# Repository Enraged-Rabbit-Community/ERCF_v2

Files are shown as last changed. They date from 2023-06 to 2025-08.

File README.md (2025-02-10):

# Enraged Rabbit Community Project

<p align="center">
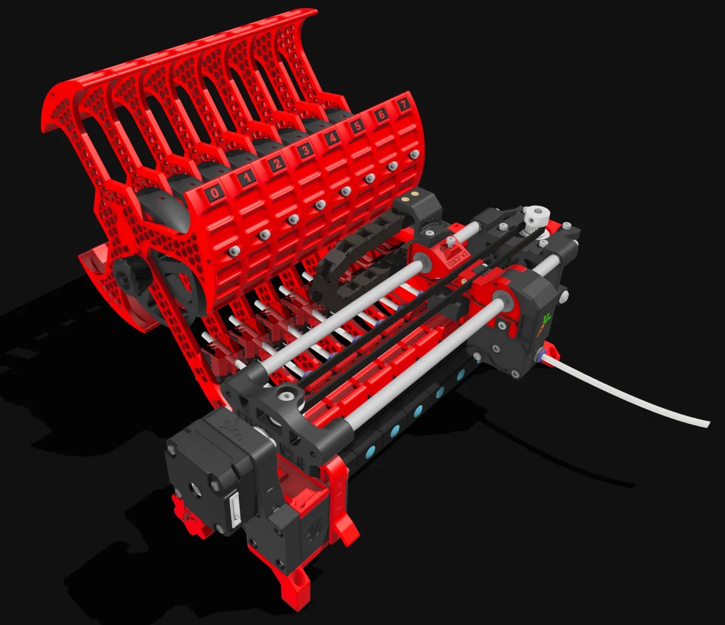
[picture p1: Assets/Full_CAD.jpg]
ERCFv2
  
  <h1 align="center">ERCF v2 - RC1</h1>
</p>

<p align="center">
An expandable MMU for Klipper-based 3D-Printers
</p>

<p align="center">
   &nbsp;
   &nbsp;
   &nbsp;
   &nbsp;
   &nbsp;
</p>

<br>

<table>
<tr>
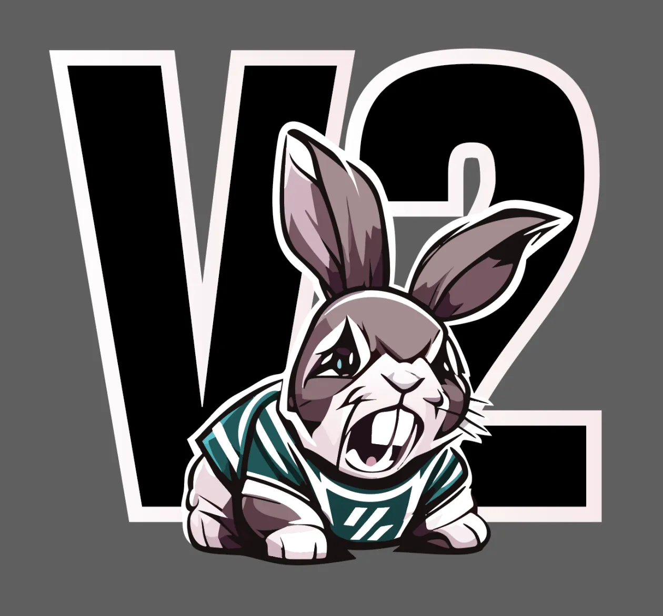
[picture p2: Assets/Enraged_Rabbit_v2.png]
RabbitV2
<td width=30%></td>
<td>
This is a community-born project and a major update to the Voron ERCF MMU that was started a couple of years ago by Ette.  It is endorsed by Ette, and the guiding philosophy wasn't to start again with a new MMU design but to refine what has already proven to be a very capable machine and push it to be the best it can be by simplifying problematic construction, improving reliability and aligning as close as possible to v1.1 BOM. However, the project includes an all-new optional integrated filament buffer system (ERCT), filament cutter option (ERF), a collection of recommended tool head sensor modifications and a bit of Bling! It fully leverages the Happy Hare firmware MMU control software with Klipper Screen extensions.
<p>
  
There is a rapidly growing list of MMUs in the marketplace, from the mass-produced "Fords" who pioneered the market to the "Toyota" that are more recent efficient engineering feat but somehow lacked soul. We consider ERCFv2 the "BMW" - a little over-engineered perhaps but distinctively cool, and you feel good driving it.  We hope you enjoy it! &nbsp;&nbsp; Videos: [Teaser](https://www.youtube.com/watch?v=U2QwvPacIUk) &nbsp; [Release](https://www.youtube.com/watch?v=EJCPerBsM3Q)
</td>
</tr>
</table>

## Table of Content
  
**[ERCF](#enraged-rabbit-carrot-feeder-ercf)**<br>
**[ERCT](#enraged-rabbit-cotton-tail-erct)**<br>
**[ERF](#enraged-rabbit-filametrix-erf)**<br>
**[Toolhead Sensor Modifications](#toolhead-sensor-modifications)**<br>
**[Firmware](#firmware)**<br>
**[Documentation](#documentation)**<br>
**[BOM](#bom)**<br>
**[CAD](#cad)**<br>
**[FAQ](#faq)**<br>
**[Acknowledgements](#acknowledgements)**<br>
**[Vendors](#vendors)**<br>
**[Changelog](#changelog)**<br>
**[Build Photos](#build-photos)**<br>
**[Showroom](#user-print-showroom)**<br>
<!--
**[FAQ](Assets/FAQ.md)
-->

<br>

## Enraged Rabbit Carrot Feeder (ERCF)
<table>
<tr>
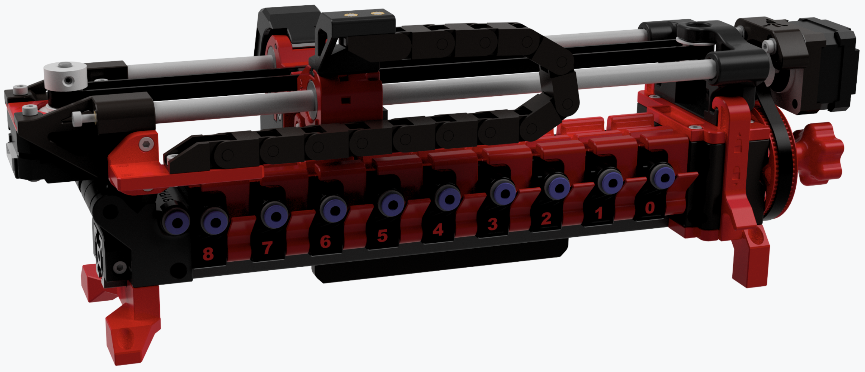
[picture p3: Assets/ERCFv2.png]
<td width=45%>An MMU or Multimaterial Unit/Upgrade allows for the automatic change of filaments on your 3D printer.  You can use it to create beautiful multi-colored prints or, if you're lazy, simply to avoid loading filament by hand. If you are familiar with ERCF v1.1, this will serve as an overview of updates:</td>
<td>
<ol>
  <li>Sturdy backbone - no more flex
  <li>Reliable (and custom) encoder design
  <li>Sprung servo instead of adjustable top hats
  <li>Innovative Filament trap in blocks instead of magnetic gates
  <li>Formal filament bypass
  <li>Reinforced gearbox assembly
  <li>Beautifully illustrated Manual
  <li>High Quality Step-by-step CAD
  <li>New integrated passive buffer system (Cotton Tail)
  <li>Perfect tips with Filametrix Filament cutter
  <li>Functional and aesthetic LED status indication
</ol>
</td>
</tr>
</table>

<br>

## Optional Enraged Rabbit Components

### Enraged Rabbit Cotton Tail (ERCT)
<table>
<tr>
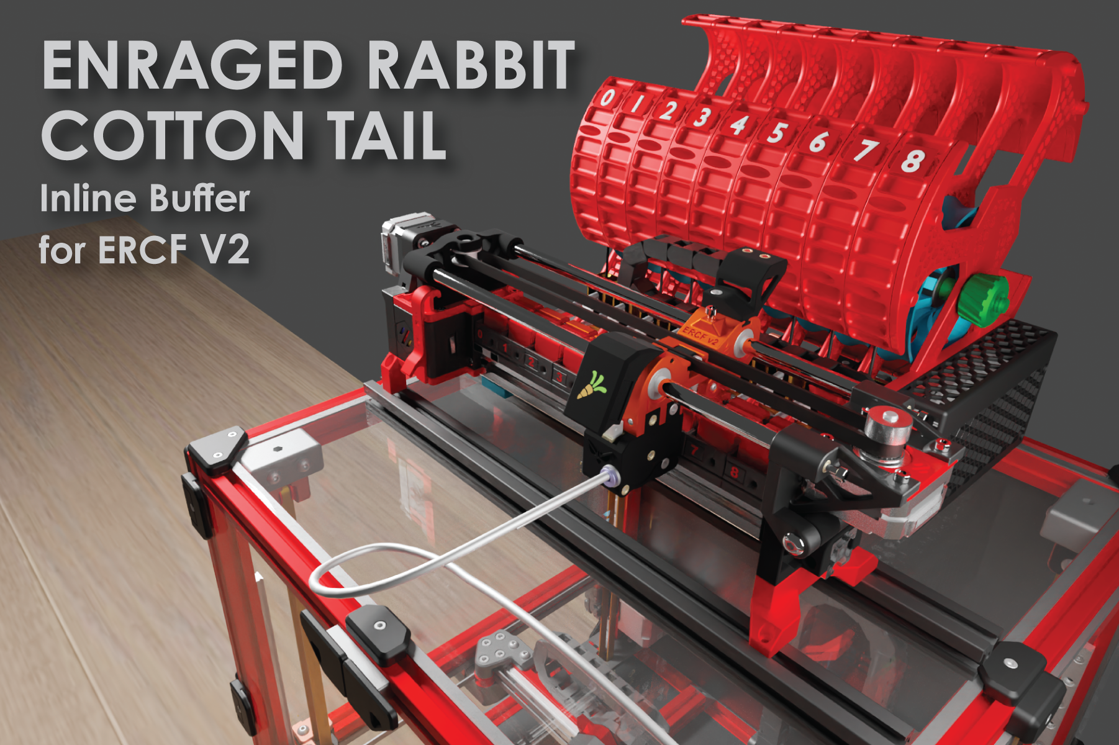
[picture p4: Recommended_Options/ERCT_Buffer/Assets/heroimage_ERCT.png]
ERCT
<td width=30%></td>
<td>
When an MMU changes tool, the unloaded filament needs to be thoughtfully managed so that it doesn't tangle. The Enraged Rabbit Cotton Tail (ERCT) buffer system is designed to attach directly to ERCF V2. It is a passive system that optimizes space and is also designed to reduce resistance in the filament path, creating a consistent system for calibration.
<p>

ERCT includes a pregate filament sensor to more reliably manage endless spools. It also incorporates a NEOpixel on each gate that, when driven by the Happy Hare firmware, provides functional feedback and the necessary "bling!" Enjoy!
<p>

[Read more](Recommended_Options/ERCT_Buffer/README.md) &nbsp;&nbsp; Videos: [Rear Loading](https://youtu.be/9jzB5Un6HKo) [Front Loading](https://youtu.be/GlSXtUkd-b8)
</td>
</tr>
</table>

<br>

### Enraged Rabbit Filametrix (ERF)
<table>
<tr>
<td>
Before the MMU can unload a filament, the tip must be prepared so that it can be cleanly loaded next time.  This tip-forming process is very difficult to tune and varies based on material type, temperature, hotend type and even weather!  Introducing Enraged Rabbit Filametrix (ERF) filament cutting system.  This lightweight addition to your Stealthburner toolhead adds a cutting blade.  When retracting, the problematic tip of the filament is simply cut off for perfect tips and no jams.
<p>

ERF also supports an optional servo operated ganrtry activation pin so no print area is lost with this addition. ERF designs also include the recommended integrated toolhead sensor
<p>

[Read more](Recommended_Options/ERF_Filament_Cutter/README.md)
</td>
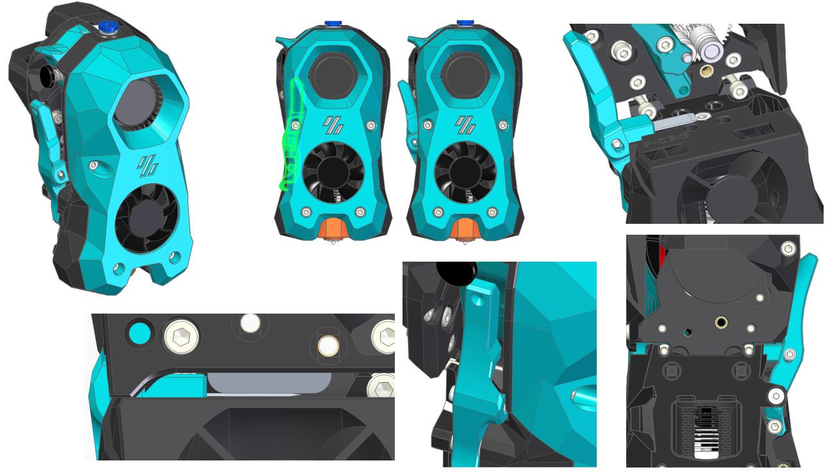
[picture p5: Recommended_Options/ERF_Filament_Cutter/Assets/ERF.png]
ERF
<td width=30%></td>
</tr>
</table>

<br>

### Toolhead Sensor Modifications
<table>
<tr>
<td>
ERCF can be operated without a toolhead sensor (filament detection) in the toolhead but it is **not recommended**. A toolhead sensor provides an accurate homing point very close to the nozzle but also adds reliability to the tool change process. ERCF includes a set of toolhead sensor modifications for popular extruders. These work reliably through coupling a microswitch to the filament path.
<p>

[Read more](Recommended_Options/Toolhead_Modifications/README.md)
</td>
</tr>
</table>

<br>

### Purge System (ERPS)
Pellet purge system to remove the need for the wipe tower. Stay tuned.

<br>

## Firmware
<table>
<tr>
<td width=30%>KlipperScreen</td>
<td>
ERCF is designed to be used with the Happy Hare MMU firmware for Klipper which adds a set of klipper extensions for configuration setup, testing and operation of ERCF. These commands are available through the command line or macros but are perhaps best operated with an interactive UI with the optional KlipperScreen extension.
<p>

Happy Hare provides an easy installation script which has knowledge of recommended settings and will greatly accelerate the setup process.
<p>

[Happy Hare](https://github.com/moggieuk/Happy-Hare/wiki) &nbsp;&nbsp; [KlipperScreen](https://github.com/moggieuk/KlipperScreen-Happy-Hare-Edition)
</td>
</tr>
</table>

<br>

## Documentation
<table>
<tr>
<td>
Building something as complex as an MMU is a challenging undertaking, but the ERCFv2 project contains an amazingly detailed and illustrated manual with step-by-step instructions.  We have tried to make the process similar to fitting together a jigsaw puzzle, albeit with a few optional pieces.
<p>

[ERCFv2 PDF Manual](Documentation/ERCF_v2_Manual.pdf)
</td>
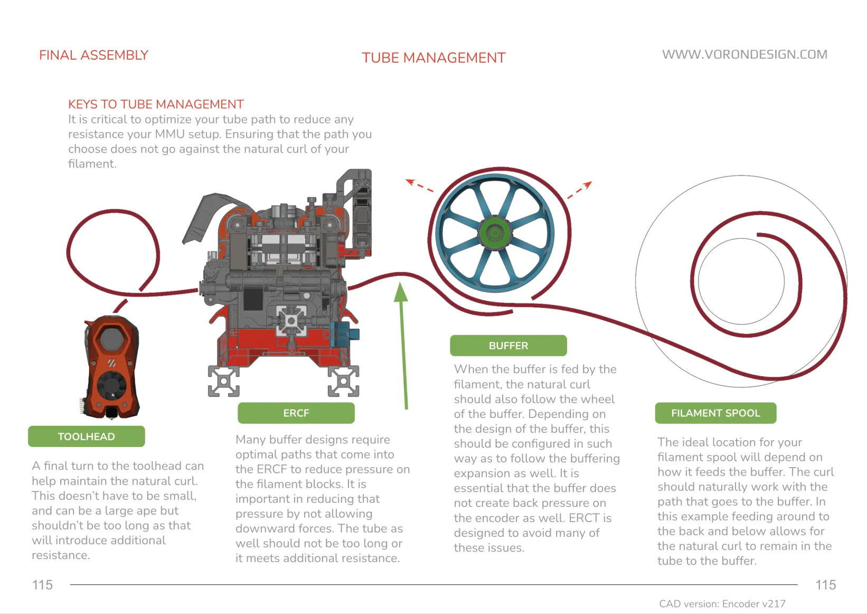
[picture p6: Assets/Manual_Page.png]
ERCF Manual
<td width=30%></td>
</tr>
</table>

<br>

## BOM
<table>
<tr>
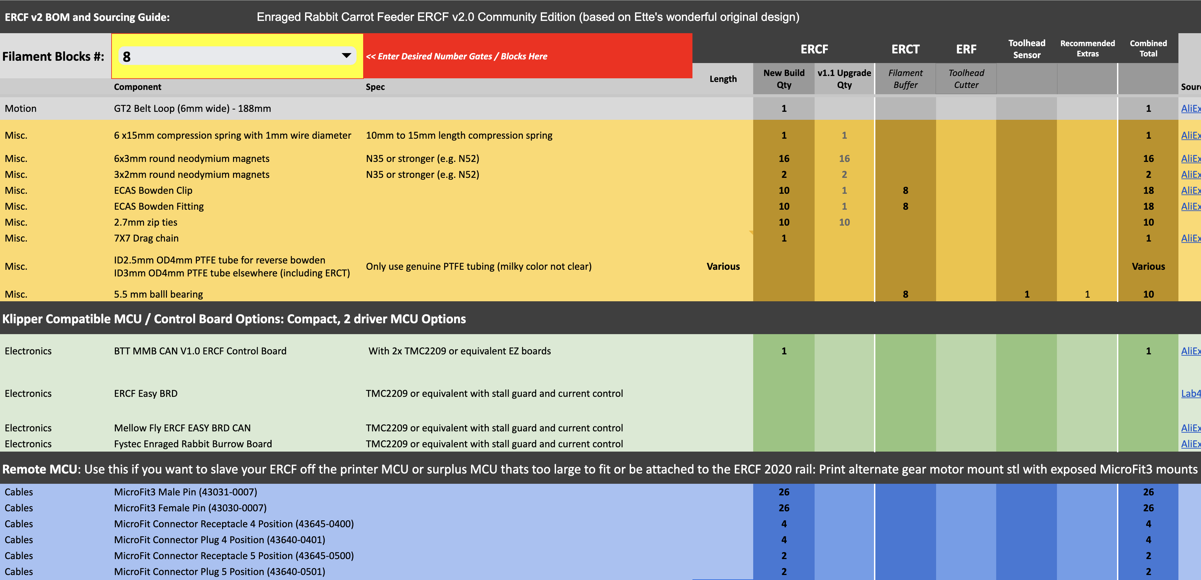
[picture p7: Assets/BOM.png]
ERCF Project BOM
<td width=30%></td>
<td>
You can find a Bill of Materials (BOM) and a convenient printed parts tracker for the project and options here. Note that the BOM also contains an upgrade list for those of you who want to use your existing ERCF v1.1 kits. Please make a copy and edit the "Filament Blocks #" to be the number of gates for your build.  This can be any number, but we encourage kit vendors to use 4/8/12 as size variations. Note that there are separate columns for core ERCF, the optional ERCT and ERF options, as well as the suggested "extras"
<p>
Please be aware that the BOM is strictly for reference. The recommended parts can be exchanged for other similar quality parts. Manufacturers who use the BOM as a reference must submit an application for certification before selling them as ERCF V2 kits. Please contact us for certification.

[BOM](https://docs.google.com/spreadsheets/d/1HtVIu4yqzS6xJQr63-JKtMAh4Xq7wbtWPFeuiCnrnnE) &nbsp;&nbsp; [Printed Parts Tracker](https://docs.google.com/spreadsheets/d/1h1bJurR6Z8Ou36c5U9cWmqI86tXKlWrcZrWrHgGN13A)
</td>
</tr>
</table>

<br>

## CAD
<table>
<tr>
<td>
A lot of work has gone into creating a quality CAD model of the project, carefully organized into folders that match the documentation!  It is highly recommended that you open the CAD and hide every folder and then expose them one at a time as you work through the build.
<p>

[Master CAD](CAD)
</td>
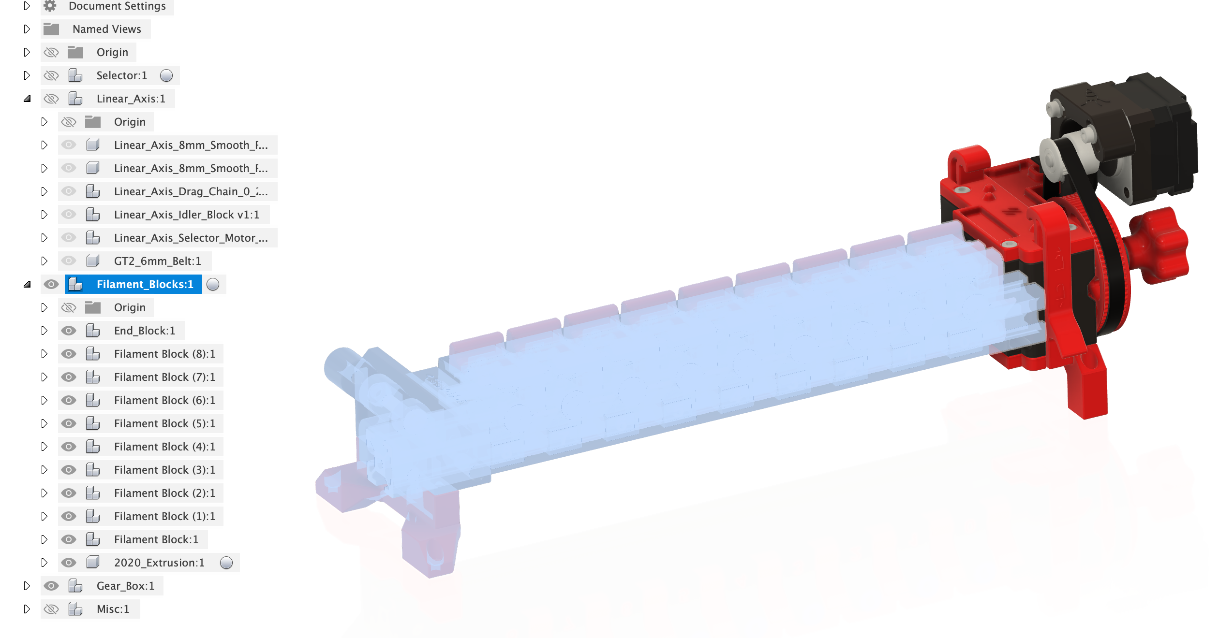
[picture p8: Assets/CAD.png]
ERCF Master CAD
<td width=30%></td>
</tr>
</table>

<br>

## FAQ
ERCF v2 is currently in the RC1 phase.  That means that we hope the BOM and parts are complete, but there are still some areas of polish needed: documentation, kit availability, etc. Therefore, we're sure there will be lots of questions.  To avoid repetition on the various support channels, you can find a list of [frequently asked questions](FAQ.md) here.  If something isn't answered the best place to go is the [ERCF Discord server](https://discord.gg/MPZ4cHm9gm)

<br>

## Acknowledgements
Most importantly let me introduce the development, test and doc team.  A project like this doesn't happen without many hundreds of hours of volunteer effort and all of these folks are truely awesome.  Please give some :clap: :clap: :clap:
<ul>
  <li>@moggieuk V0.1503 | V2.4088 (Mr Happy Hare & Chief whip)
  <li>@gneu V2.5345 (Filament block & bling innovator)
  <li>@sneakytreesnake V2.3804 (The project backbone!)
  <li>@mneuhaus VT.483 (Mr Binky)
  <li>@Miriax (Designer & Doc Demon)
  <li>@kinematicdigit VS.744 (Mr Cotton Tail & Doc Illustrator)
  <li>@ningpj (Tester, Breaker & Documenter)
  <li>@fizzy (King of CAD)
  <li>@gsx8299 (Test Builder Extraordinaire)
  <li>@sorted (Filametrix "don't get enraged" filament cutting system)
  <li>@kierantheman (Mr ThumperBlocks)
  <li>@Fragmon (Videographer)
  <li>@Silverback V2.1356 (Filametrix tester, builder & engineer)
</ul>

<br>

## Vendors
<table>
<tr>
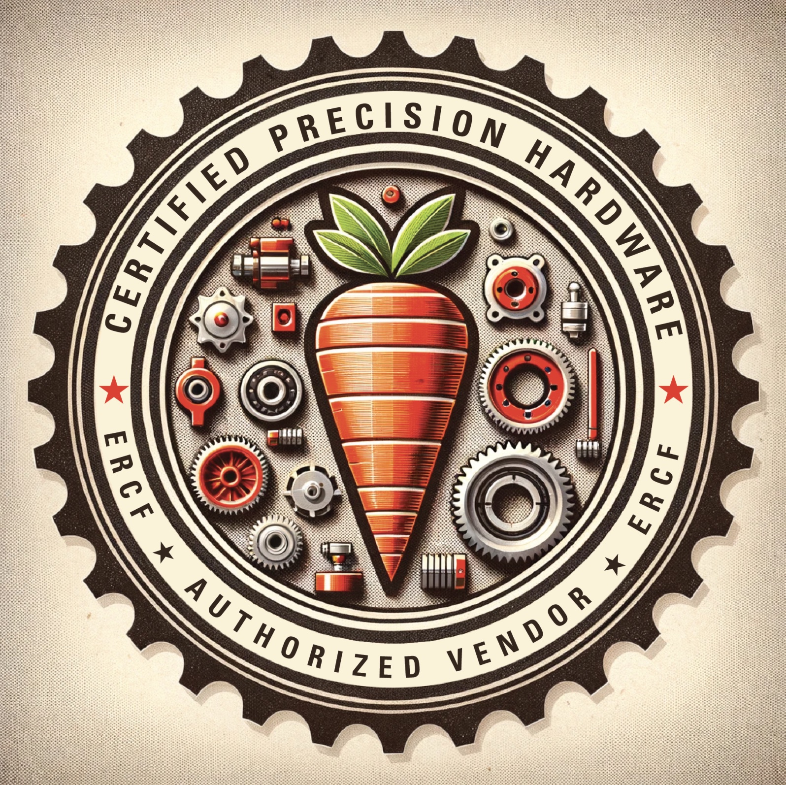
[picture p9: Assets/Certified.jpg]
Vendor Certification
<td width=25%></td>
<td>
These kits and specialty parts will have been checked by us and meet good quality standards. Pending Certification means it has met our first pass inspection and in the process of being verified as a V2 kit. <strong>WE DO NOT RECOMMEND PURCHASING KITS WITHOUT THE CERTIFICATION BY US. PLEASE CHECK BACK HERE FOR THE LIST OF AUTHORIZED VENDORS AND MANUFACTURERS</strong>:<br>
<p>
<ul>
  <li> <strong>Certified - Siboor</strong>
  </li>
  <li> <strong>Certified - Triangle Labs</strong>
  </li>
  <li> <strong>Certified - Seleadlabs</strong>
  </li>
  <li> <strong>Certified -  Makerpanda</strong>
  </li>
  <li> <strong>Certified -  Fysetc</strong>
  </li>
  <li> Pending Certification - LDO Motors
  </li>
  <li> <strong>Certified - Dodo 3D Labs</strong>
  </li>

  <br>
  <p>
  A list of more official and certified vendors is on the way... stay tuned!
</td>
</tr>
</table>

**Manufacturers:**
_If you want to be included, please contact us. We are happy to validate your kit/parts and then add you to the list._

<br>

## Changelog
<ul>
  <li>v2.0 rc1 - Initial Release (Merry Christmas!)
</ul>

CAD Design Guidelines used in this project (in case you were interested) can be found: [here](/Assets/Dev_Notes.md).

<hr>

<p align="center"><i>
There once was a printer so keen,<br>
To print in red, yellow, and green.<br>
It whirred and it spun,<br>
Mixing colors for fun,<br>
The most vibrant prints ever seen!
</i></p>

<br>

## Build Photos












<br>

## User Print Showroom
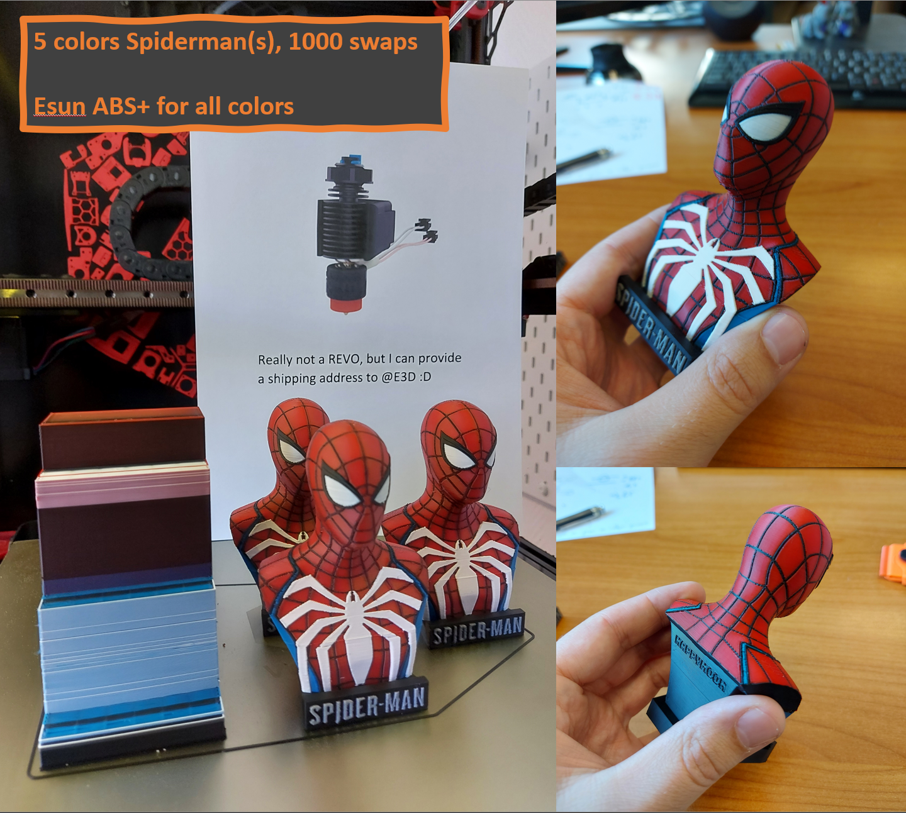
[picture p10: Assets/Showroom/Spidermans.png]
Spidermans
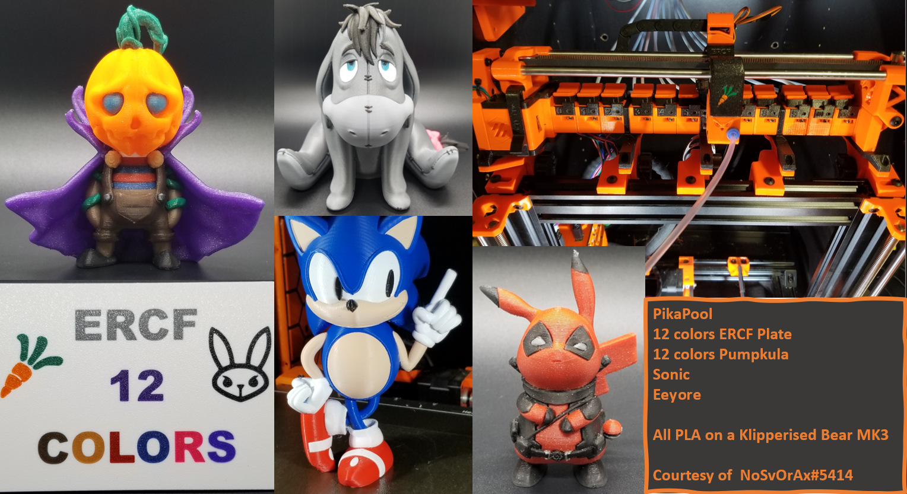
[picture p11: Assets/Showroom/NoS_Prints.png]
NoS_prints
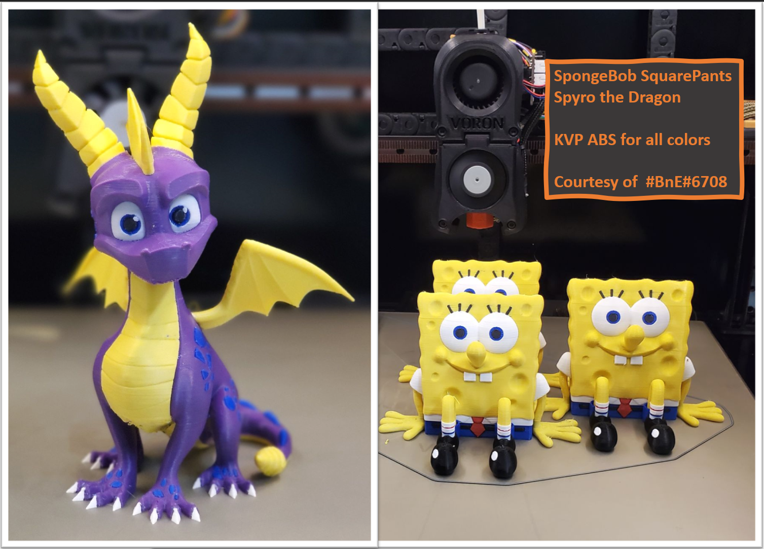
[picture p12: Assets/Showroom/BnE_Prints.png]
BnE_Prints
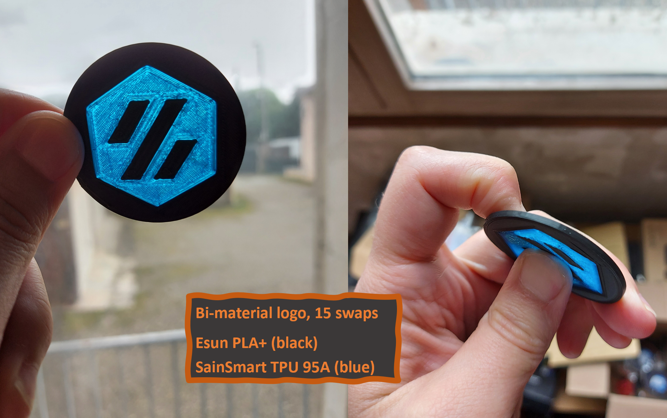
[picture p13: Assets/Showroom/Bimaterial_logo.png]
Voron Logo TPU
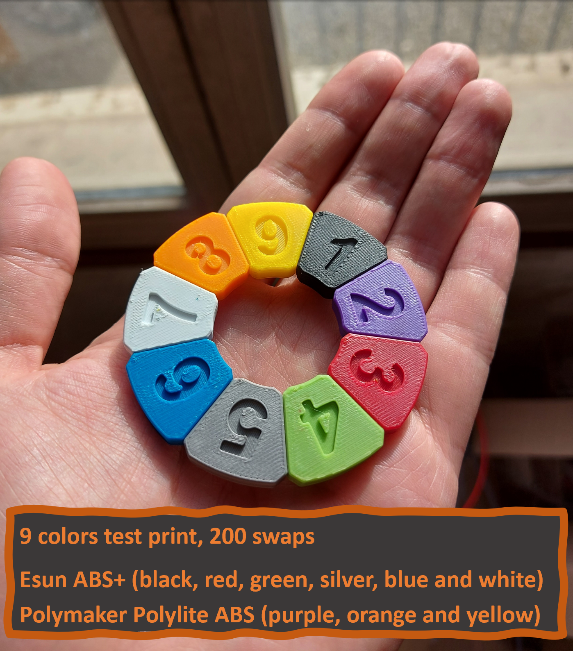
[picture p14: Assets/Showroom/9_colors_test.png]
9_colors_test


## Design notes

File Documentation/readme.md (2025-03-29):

# ERCF Quickstart

Follow the steps on these pages in order to set up ERCF for the first time!

### ERCF Setup Steps:
- [Flashing Your Local MCU](https://github.com/Enraged-Rabbit-Community/ERCF_v2/blob/master/Documentation/Flashing-Local-MCU.md)
- [Installing Happy Hare](https://github.com/Enraged-Rabbit-Community/ERCF_v2/blob/master/Documentation/Installing-Happy-Hare.md)
- [Happy Hare Configuration](https://github.com/Enraged-Rabbit-Community/ERCF_v2/blob/master/Documentation/Happy-Hare-Configuration.md)
- [Hardware Configuration Checks](https://github.com/Enraged-Rabbit-Community/ERCF_v2/blob/master/Documentation/Hardware-configuration-checks.md)
- [Hardware Calibration](https://github.com/Enraged-Rabbit-Community/ERCF_v2/blob/master/Documentation/Hardware-Calibration.md)
- [Toolhead Distances](https://github.com/Enraged-Rabbit-Community/ERCF_v2/blob/master/Documentation/Toolhead-Distances.md)
- [Installing KlipperScreen Happy Hare](https://github.com/Enraged-Rabbit-Community/ERCF_v2/blob/master/Documentation/Installing-KlipperScreen.md)
- [Slicer Setup](https://github.com/Enraged-Rabbit-Community/ERCF_v2/blob/master/Documentation/Slicer-Setup.md)
- [Further Mods to Consider](https://github.com/Enraged-Rabbit-Community/ERCF_v2/blob/master/Documentation/Further-Mods.md)

#### Even more Happy Hare info can be found at:
- [Happy Hare Wiki](https://github.com/moggieuk/Happy-Hare/wiki)

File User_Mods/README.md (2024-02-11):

# User mods

## Summary and Links

**Gneu42**
* [Block End with Bushing](Gneu42/Block_End_with_Bushings)
* [Drag chain Anchor with connectors](Gneu42/Drag_Chain_Anchor_With_Microfit3)
* [Selcetor Drag chain Anchor with servo connectors](Gneu42/Selector_Drag_chain_Anchor_with_servo_connectors)
* [Apron Leds Blank cover](Gneu42/Apron_Leds)

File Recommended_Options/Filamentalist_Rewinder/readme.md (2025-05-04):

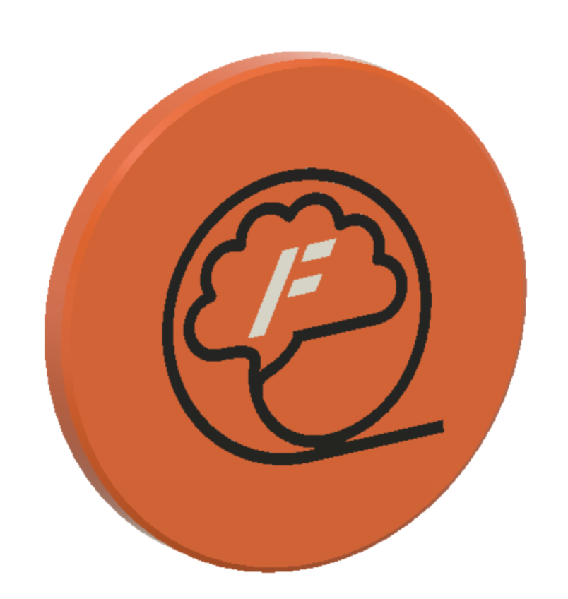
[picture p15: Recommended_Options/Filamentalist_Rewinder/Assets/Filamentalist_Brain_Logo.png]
<p align="center">
<h1 align="center">The "Filamentalist" Passive Filament Driven Rewinder</h1>

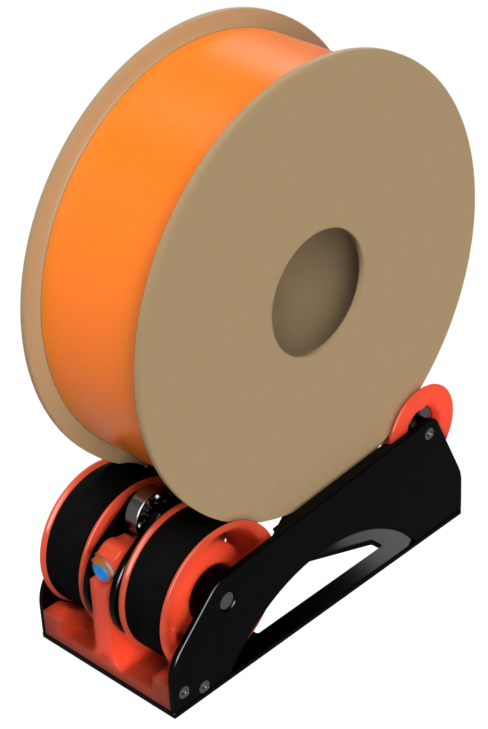
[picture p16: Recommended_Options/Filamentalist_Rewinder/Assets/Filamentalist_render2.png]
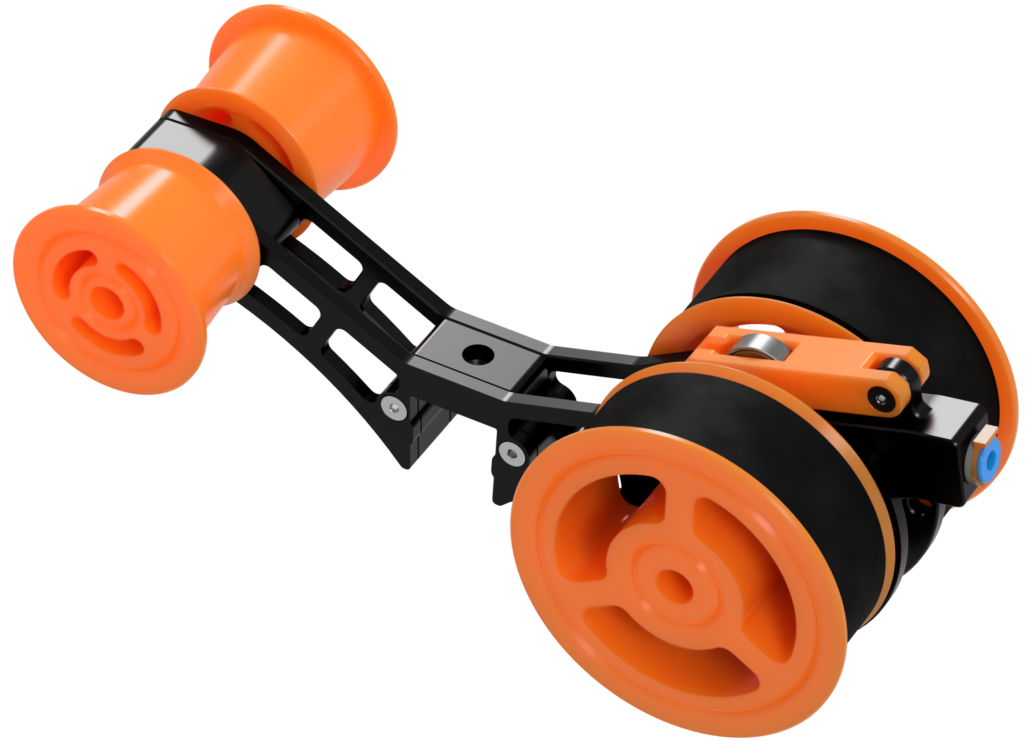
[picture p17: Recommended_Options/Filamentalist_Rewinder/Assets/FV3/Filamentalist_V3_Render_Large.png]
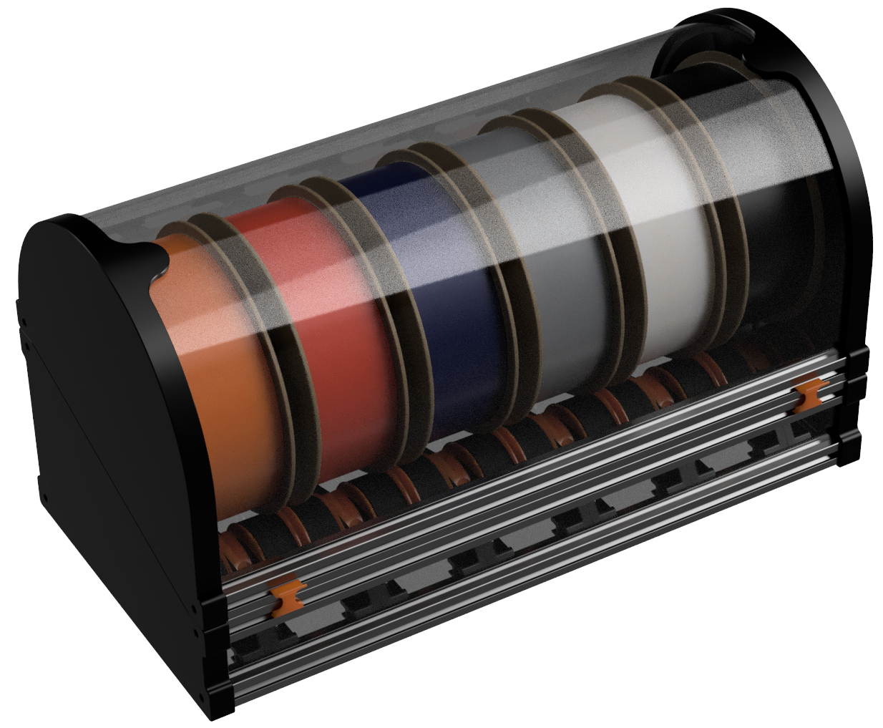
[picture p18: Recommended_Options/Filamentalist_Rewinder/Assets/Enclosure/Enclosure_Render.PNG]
[](https://github.com/Enraged-Rabbit-Community/ERCF_v2/tree/master/Recommended_Options/Filamentalist_Rewinder/Filamentalist_Classic_Rewinder)[](https://github.com/Enraged-Rabbit-Community/ERCF_v2/tree/master/Recommended_Options/Filamentalist_Rewinder/Filamentalist_FV3_Rewinder)[](https://github.com/Enraged-Rabbit-Community/ERCF_v2/tree/master/Recommended_Options/Filamentalist_Rewinder/Filamentalist_Enclosure)
</p>
   
## _____ [Filamentalist "Classic"](https://github.com/Enraged-Rabbit-Community/ERCF_v2/tree/master/Recommended_Options/Filamentalist_Rewinder/Filamentalist_Classic_Rewinder) _________ [Filamentalist FV3](https://github.com/Enraged-Rabbit-Community/ERCF_v2/tree/master/Recommended_Options/Filamentalist_Rewinder/Filamentalist_FV3_Rewinder) ___________[Filamentalist Enclosure](https://github.com/Enraged-Rabbit-Community/ERCF_v2/tree/master/Recommended_Options/Filamentalist_Rewinder/Filamentalist_Enclosure) ____
</p>

## Filamentalist Discord group [here:](https://discord.gg/zHGH9sXFVK) ##

##  Description & Theory of operation:

The Filamentalist is a passive (no motors or electronics required) integrated buffering and spool holding multi-material unit (MMU) solution.  It provides space savings and potential filament path reduction that comes with using paths from spool to buffer to MMU.

- The Filamentalist uses the axial force delivered by the MMU gear motor along the filament to load and unload to and from the filament spool.
- An adjustable spring clamp forces the filament against two o-rings that sit on the drive pulley to create a high traction interface for rotating the axle and filament spool.
- A one-way clutch style bearing locks against the drive shaft and rotates the filament spool to take up filament during an unload.
- For loading and print extruding, the clutch disengages allowing for effective free-spooling of the filament spool similar to a roller style spool holder.
- The difference in diameter of the filament driven clutched roller versus the larger rim roller that the filament spool sits on provides the needed gear ratio to produce enough rotations to take up, and unload a nearly empty or full filament roll.
- During unloading/buffering, to account for the varying diameter of a spool from full to empty, filament tension will cause the spring loaded arm to lift a small amount and release traction from the o-rings allowing slip to occur between the filament and the o-ring interface of the rewinder producing a dynamic, continuously modulating variable gear ratio (full spool = max slip, empty spool = no/minimal slip).

<p align="center">
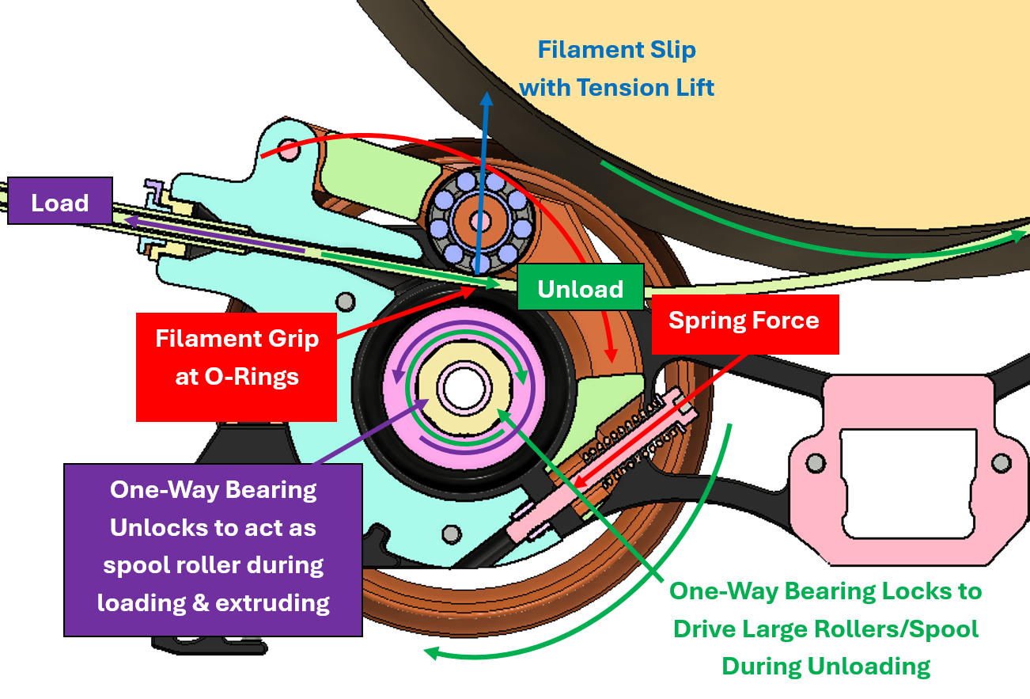
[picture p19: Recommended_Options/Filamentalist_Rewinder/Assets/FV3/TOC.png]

</p>

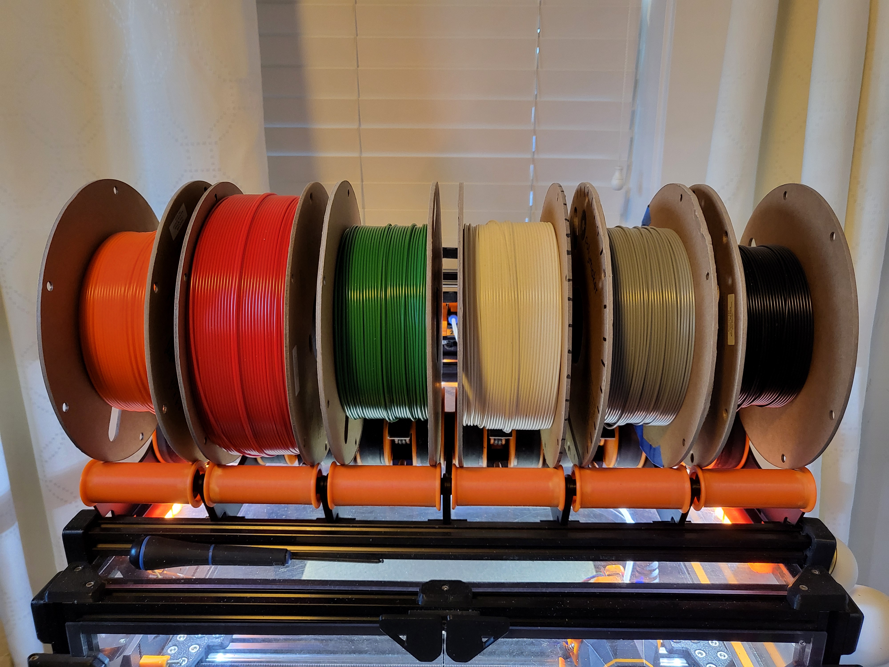
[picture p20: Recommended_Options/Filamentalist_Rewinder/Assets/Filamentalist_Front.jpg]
<p align="center">
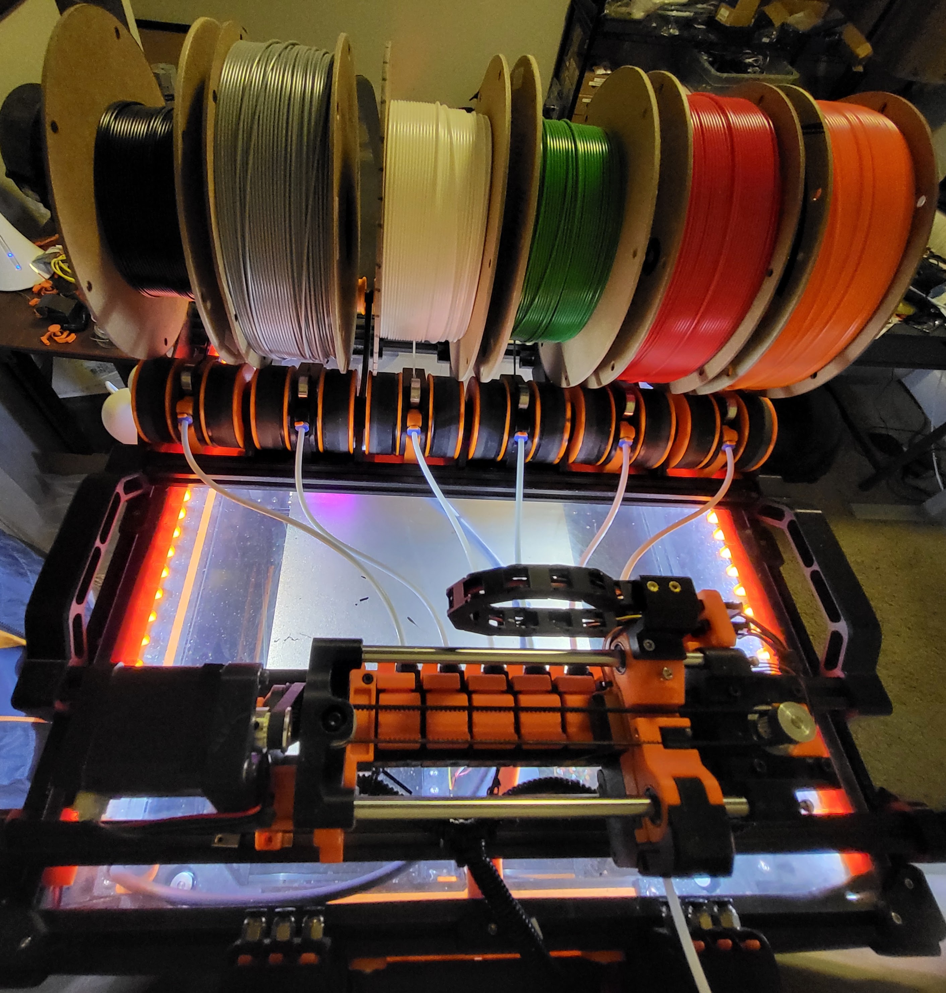
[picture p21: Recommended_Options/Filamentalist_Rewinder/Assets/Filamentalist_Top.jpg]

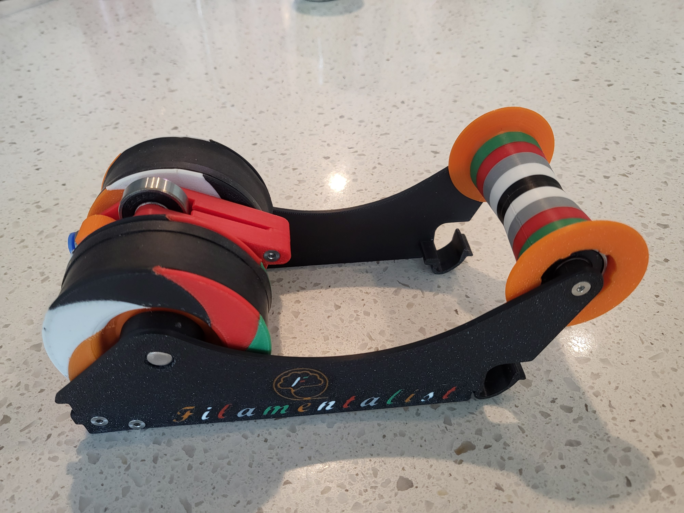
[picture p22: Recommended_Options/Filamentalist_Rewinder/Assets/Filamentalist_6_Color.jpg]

</p>

## Filamentalist Version Selection ##

One version is not necessarily better than the other.  The Filamentalist Classic has slightly better Tensioner system geometry making it a bit smoother in the filament grip/slip modulation.  The FV3 is "sexier" and accomodates wider spool widths in less horizontal space which can be useful for fitting in existing enclosures or across the top of a printer.  Below is a selection table to help with your decision.

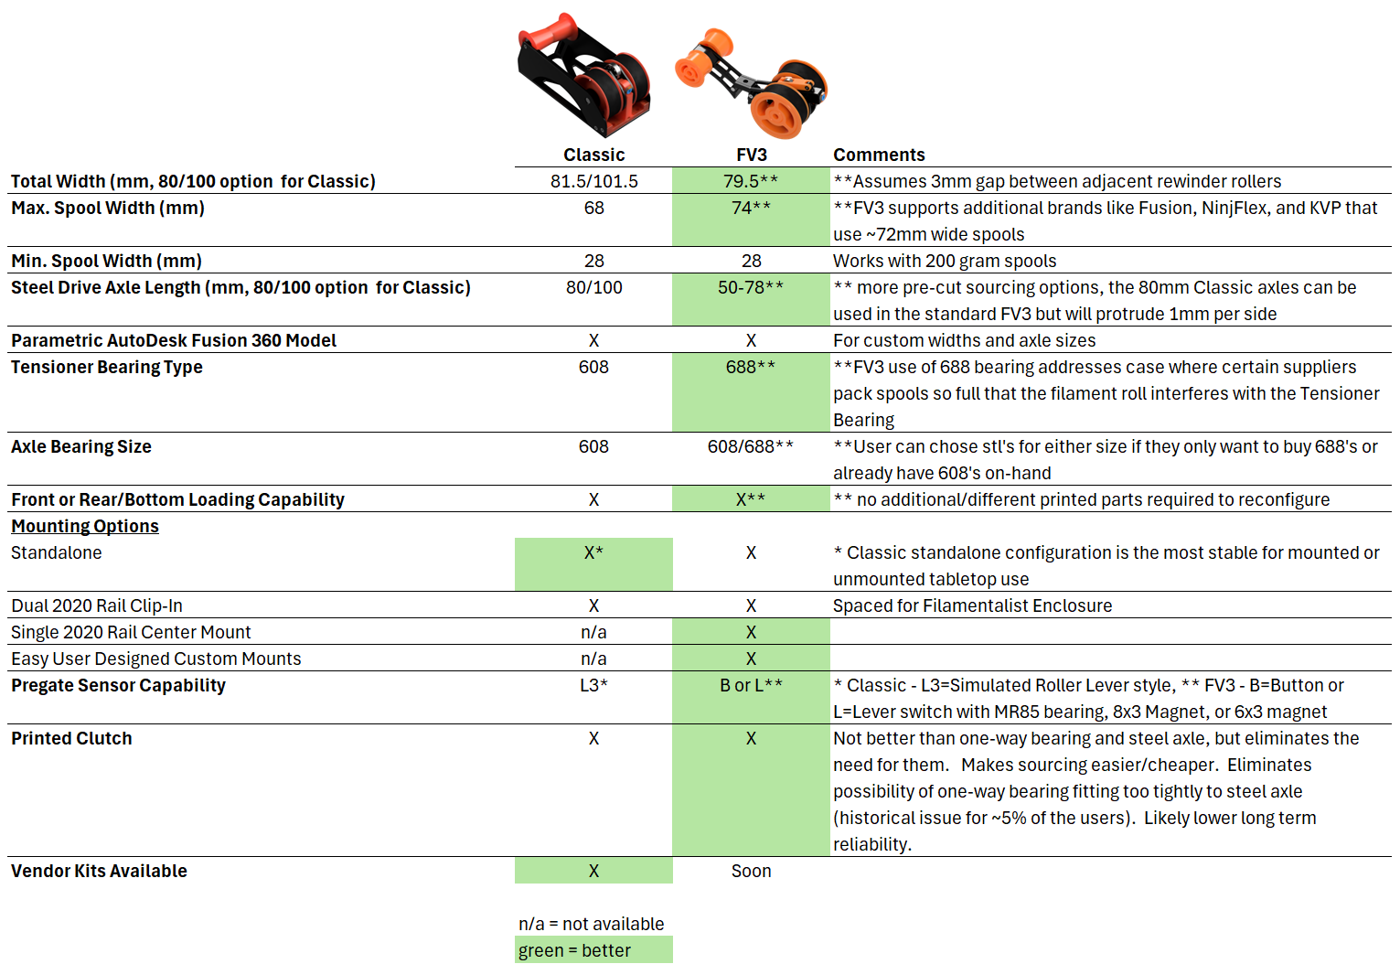
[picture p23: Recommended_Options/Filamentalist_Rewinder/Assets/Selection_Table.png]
<p align="center">

## Video of 6 rewinders swapping (plus SW Only Blobifier Purging):  [](https://photos.app.goo.gl/hKso7JYPZcdRLKrW8)

## [Video of loading a spool (pre-gate sensors auto-detect filament and pull into ERCF):](https://photos.app.goo.gl/yGS7Rr49dFMvjNLF9)  [](https://photos.app.goo.gl/yGS7Rr49dFMvjNLF9)

##  Credits:
Discord user Thisiscam first made me aware of [Muzi Xiaoyang's video](https://www.bilibili.com/video/BV1ZM41197fX/?spm_id_from=333.337.search-card.all.click) of a filament driven rewinder .  Through a long collaboration with Thisiscam, a great Beta dev/test team, and many design iterations/improvements on the Muzi Xiaoyang design, the Filamentalist was born. Key changes to the Muzi Xiaoyang design include incorporation of a one-way bearing, establishing the correct gear ratio for operation across the range of empty-to-full spools, and the long-life o-ring based filament clamping interface.

A special mention and thanks goes out to Cheesefrog and JCPhlux for their innovation and inputs for design refinement. 

##  **Additional Notes/Considerations** 

Things that you need to know include:
1. Due to continual evolution of the design based on user feedback, the pictures in the readme files and documentation may not always reflect the most current designs.  They will be similar and generally represent the latest parts and assemblies.
2. There are multiple options for the Filamentalist.  Determine which versions/options you want and select the stl's to print accordingly.  If you use Autodesk Fusion 360 there is parametric models available for both the Classic and FV3 rewinders that will allow customization for unique widths and axle lengths. Please see the Selection Aid table above to help choose.
3. If you're using, or upgrading from a ERCFv1 or v2 version you may want/need a higher torque gear motor.  Many in the Beta team ran NEMA 17's spec'd at 55 N-cm max torque and config'd them for 1-1.5A (probably overkill...).  If running the ERCF V1 or V2 with the 80 tooth gear Grafton's [40 Tooth NEMA 17 Mod](https://www.printables.com/model/692720-ercf-40-tooth-gear-modifiction) is a good modification for gaining more speed from a motor with 40N-cm torque or greater.  This may not be required so if you already have built your ERCF, try the Filamentalist with the motor/gearing you have and decide if you think you need more torque/speed.
4. Because the standard tuning of this design relies on some filament slip at the o-rings, the o-rings may ultimately wear-out.  Testing and extrapolation estimates that the wear-out point is  greater than 5K cycles. See the O-Ring Replacement section in the assembly manuals for o-ring swap/replacement instructions. 
5. Due to pressfits for the axle bearings and ECAS fitting, printer calibration is important.  Calibration "Test Block" stl's are included in the projects/CAD.  It is recommended you print the calibration tool first and test the press fits, M3 thread cutting, M3 slip fit, filament path holes to determine if you need to apply any scaling or changes to your extrusion factors in your slicer before printing.  Due to varying ECAS supplier tolerances and varying printer tolerances some experienced cracking at the ECAS hole when pressing in the ECAS.  If all other press fits work well on the calibration tool but you experience cracking at the ECAS hole when pressing in an ECAS fitting, you can use an Xacto knife to lightly remove some plastic from the ECAS hole.  If the ECAS is too loose you can use superglue to glue the ECAS into the Tensioner Mount (not the Test Block 😉 ).
6. Questions or input?
   - Refer to the [FAQ](https://github.com/Enraged-Rabbit-Community/ERCF_v2/blob/master/Recommended_Options/Filamentalist_Rewinder/Filamentalist_FAQ.md)
   - [Troubleshooting Guide](https://github.com/Enraged-Rabbit-Community/ERCF_v2/blob/master/Recommended_Options/Filamentalist_Rewinder/troubleshoot.md)
   - Filamentalist Discord group [here:](https://discord.gg/zHGH9sXFVK)

##  Tuning

Tune by setting the Tensioner Arm clamping force.  The arm does not need an extreme amount of tension.  To tune the spring force, lift the tensioner and insert a section of filament through the o-ring bearing interface and into the bowden tube.  Hold a Rim Roller to keep it from rotating and try to pull the filament out (in unload direction).  You want the slip force to be slightly more than what the overall system drag is, so you have to imagine the range of gear motor pull force vs rewinder drag and set a slip range in-between the two "imaginary" lines.  As a starting point adjust the spring tensioner screw accordingly and err on the light side.  Run the rewinder (see test code below). If loose filament is forming around the filament spool during unload, tighten the spring tensioning screw.  If no loose filament is forming around the filament roll, gradually reduce the spring tension until loose filament starts to accumulate and then increase tension in ~1/2 screw turn increments until you feel you have the lightest tension that results in a tightly packed unload. 

##  Testing

Below are macros you can cut and paste into the bottom of your mmu_software.cfg or printer.cfg to test and tune your rewinders.

Happy multi-material printing and rewindering!

```
[gcode_macro rewinder_test]
gcode:
    {% set tool = params.TOOL | default(0) | int %}   ; This target can be set with the drop-down in Mainsail
    {% set cycles = params.CYCLES | default(5) | int %}   ; This target can be set with the drop-down in Mainsail
    {% set speed = params.SPEED | default(300) | float %}   ; This target can be set with the drop-down in Mainsail
    {% set accel = params.ACCEL | default(300) | float %}   ; This target can be set with the drop-down in Mainsail
    {% set length = params.LENGTH | default(800) | float %}   ; This target can be set with the drop-down in Mainsail

    MMU_SELECT TOOL={tool}
    MMU_PRELOAD
    MMU_TEST_LOAD LENGTH=50
    {% for n in range(cycles) %}

        MMU_SERVO POS=DOWN
        MMU_TEST_MOVE SPEED={speed} ACCEL={accel} MOVE={length}
        MMU_SERVO POS=UP
# to stop a macro mid-cycle you must use the e-stop.  This dwell allows you to hit the e-stop while the servo is up so that you can pull the filament out of the ERCF while the printer/macro is stopped
        MMU_SERVO POS=DOWN
        MMU_TEST_MOVE SPEED={speed} ACCEL={accel} MOVE=-{length}
        MMU_SERVO POS=UP

    {% endfor %}

    MMU_UNLOAD

```

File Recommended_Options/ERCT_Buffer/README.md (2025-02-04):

# Enraged Rabbit Cotton Tail

<p align="center">
  ERCT
</p>

## Introduction

The Enraged Rabbit Cotton Tail (ERCT) buffer system is designed to attach directly to ERCF V2. It is also designed to reduce as much resistance as possible in the filament path, creating a consistent system for calibration.

This system is also designed to reduce the buffer length, while the loops are defined by the amount of tube you use from the encoder to the tool head. This is calculated by the total Bowden tube length divided by 225.  QoL features also allow for illuminated coupler blocks to indicate filament states.

**Features include:**

* Large central buffer wheel - reduces the bend radius of the filament's natural shape - each wheel comes pre-notched to make loading filament easier.
* Inline connection - connects directly to the 2020 extrusion arm
* Short Buffer Length - Can operate as short as 500mm in buffer Length
* Stackable Arm - Each arm is stackable for whatever combination of gates you want. They are optimized for strength and lightweight while providing loading and unloading filament access. More than 12 channels will require self-sourcing a metal axle rod, but printing your own up to 12 channels is available in the STL directory.
* Uses most parts from ERCP V1 -  if you already have a kit, most parts should be interchangeable.

##

***

## Acknowledgements

ERCT was designed to simplify the buffer design and integrate cleanly with ERCFv2. I thank the entire team from the ERCF V2 team, especially Moggie, for bringing me onto the team. I also have my home server, Fizzy's Tech, on Discord to thank for the countless support and hosting of the Beta development on that server. Jose from Fizzy's Tech was instrumental in this development as he was part of the system's early development and early testing. There are numerous testers who have helped as well, making suggestions throughout the beta cycle. I want to give a special shout-out to Wolffy01 and gsx8299 for their contributions to ideas, testing and mods.&#x20;

Questions related to this buffer can be directed at <https://discord.com/channels/460117602945990666/909743915475816458> or you may visit my home server at <https://discord.gg/Gs2vAtK7T7>

Terrance Lam
@kinematicdigit
###

***

### BOM (Each arm group/channel):

* (4) 8mm M3 screws
* (1) 16mm M3 screw
* (1) M3 threaded inserts (M3x5x4mm) Heat Sets
* 48.5mm PTFE Tubing (4mm OD/3MM ID Clear)
* (1) 608 ZZ Bearing (same as ERCP - skateboard bearings will work as well)
* (2) ECAS
* (1) M3 Roll-in Spring T-nut (for attaching to 2020 extrusions)

### End cap (with integrated MMB CASE) needs:

* (5) 8mm M3 screws
* (4) M3 threaded inserts (M3x5x4mm) Heat Sets

* (1) BTT MMB Can board
* (1) Microswitch per arm
* (1) 5.5 mm ball bearing per arm
* (2) 8 or 10 mm M2 self-thread screws per arm
* (1) Button Neopixels per arm
***

**FULL BUILD INSTRUCTIONS FOUND IN THE ERCF V2 BUILD GUIDE**

**LOADING THE BUFFER**

There are several ways to load the buffer. Use this as a reference but you may find other ways to load that is easier for you.

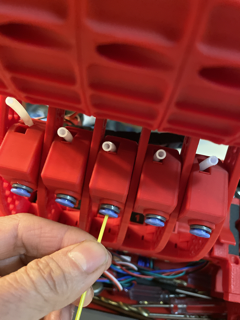
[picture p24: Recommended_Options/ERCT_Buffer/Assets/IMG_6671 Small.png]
|  | To load the buffer, filament from your reverse Bowden. Try your best to work with the natural curl of the filament and feed it till you see it pop out on top. |
| ---: | :--- |
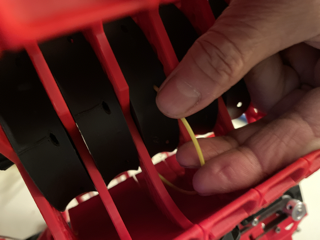
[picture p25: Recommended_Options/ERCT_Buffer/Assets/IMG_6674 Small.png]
|  | Grab it from up top, and curl it back into one of the multiple filament loading holes located along one side of the buffer wheel. |
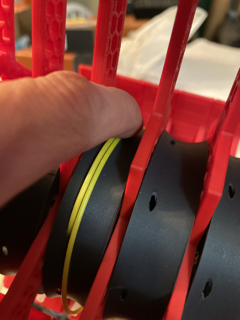
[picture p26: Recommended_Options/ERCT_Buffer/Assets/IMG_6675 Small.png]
|  | Turn the wheel until you have the number of rows needed for your tube length between the ERCF encoder and the tool head (to calculate the right length, measure the tube and divide by 230mm. This will equal the number of rows you need to wrap around the wheel - maximum of 7). |
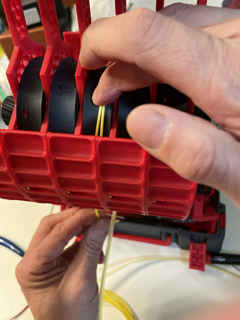
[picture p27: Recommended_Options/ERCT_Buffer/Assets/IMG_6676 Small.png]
|  | Back below, grab the filament on the wheel and pull it out. |
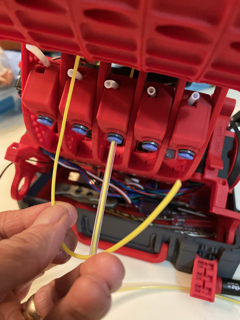
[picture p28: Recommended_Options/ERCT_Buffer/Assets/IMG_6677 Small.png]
|  | Give yourself some length (about 30 cm). |
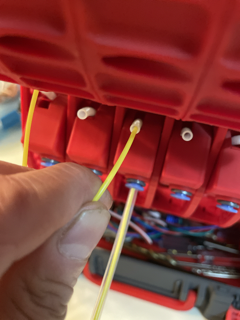
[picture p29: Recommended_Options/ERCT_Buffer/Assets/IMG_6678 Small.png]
|  | Feed back into the tube located there. |
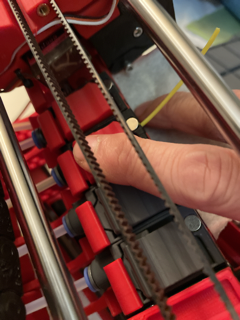
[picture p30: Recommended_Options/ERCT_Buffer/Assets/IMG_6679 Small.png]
|  | It will feed through, and you should feel some resistance from the trap; press on the top hat to help it through. |
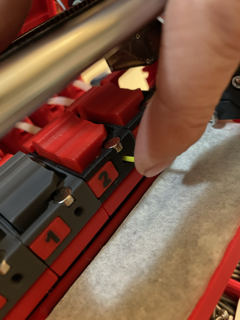
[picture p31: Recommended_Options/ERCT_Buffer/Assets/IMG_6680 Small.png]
|  | The final step is to push the filament flush to the opening so it doesn’t catch on the selector. That’s it. Load it all up, and away you go! |

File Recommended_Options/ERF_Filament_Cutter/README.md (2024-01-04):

# Enraged Rabbit "Filametrix" Filament Cutter
<table>
  <tr>
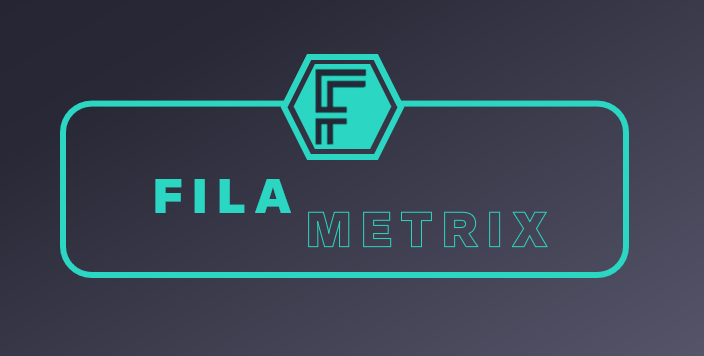
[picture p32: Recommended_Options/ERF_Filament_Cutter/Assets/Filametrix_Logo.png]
ER Filametrix
    <td width=30%></td>
    <td>
      This options adds a lightweight filament cutting capability to the Voron Stealthburner CW2 toolhead for perfect filament tips without having to tune the traditional tip forming process. Thanks to contributors it supports a number of different hotends. This can lead to much greater reliability of your MMU.  We hope over time to offer support for additional toolheads.
    </td>
  </tr>
</table>

<br>

## Illustration

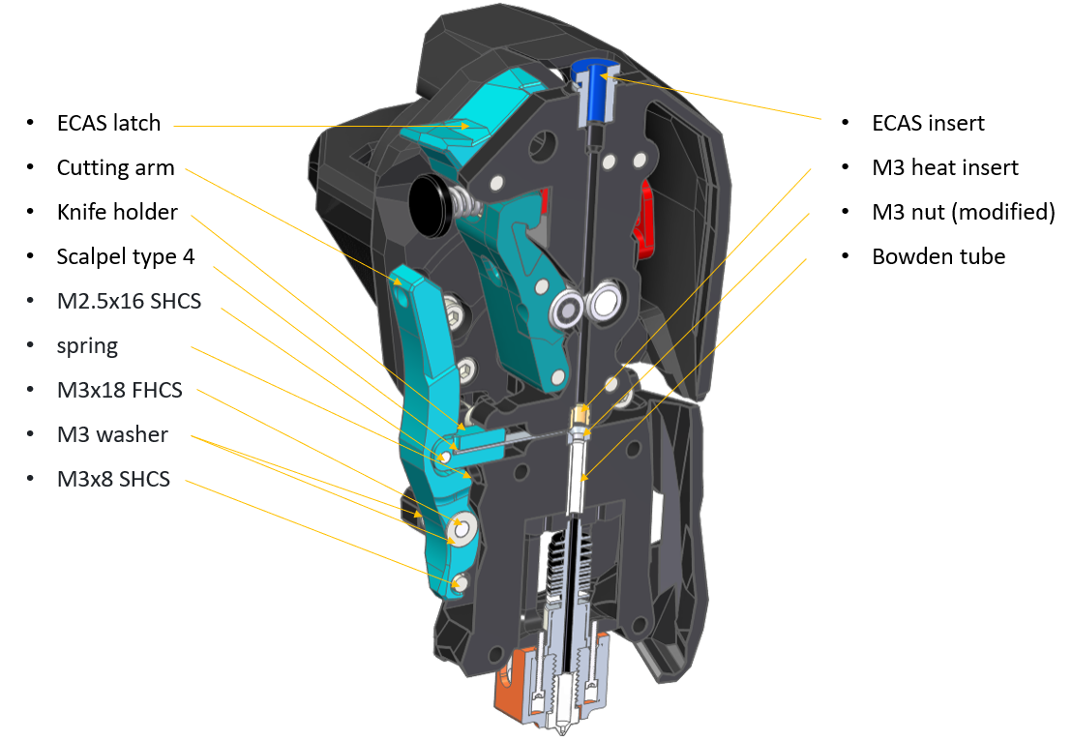
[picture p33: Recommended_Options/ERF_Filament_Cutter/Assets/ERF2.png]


## Toolheads
Currently ERF is only available for the Stealthburner toolhead. We hope to offer other options in the future. When choosing toolhead sensors "types" refer to the explanation of options [here](/Recommended_Options/Toolhead_Modifications/README.md#possible-options-explained).

### Supported Extruders for StealthBurner and Sensor Options
<table>
  <tr>
    <th>Extruder</th>
    <th>Sensor Option</th>
    <th>STLs</th>
    <th>Credit</th>
  </tr>
  <tr>
    <td rowspan="4">Clockwork2 (CW2)</td>
    <td>1_Toolhead_And_Entry_Sensors</td>
    <td><a href="Stls/1_Toolhead_And_Entry_Sensors/SB_CW2_Body.stl">Body</a></td>
    <td rowspan="4">Credit: <a href="https://github.com/juliusjj25">juliusjj25</a></td>
  </tr>
  <tr>
    <td>2_Toolhead_Sensor (EBB Board)</td>
    <td><a href="Stls/2_Toolhead_Sensor/SB_CW2_Body_EBB.stl">Body</a></td>
  </tr>
  <tr>
    <td>3_Entry_Sensor</td>
    <td><a href="Stls/3_Entry_Sensor/SB_CW2_Body.stl">Body</a></td>
  </tr>
  <tr>
    <td>4_No_Sensors</td>
    <td><a href="Stls/4_No_Sensors/SB_CW2_Body.stl">Body</a></td>
  </tr>

  <tr>
    <td>LGX Lite</td>
    <td>4_No_Sensors</td>
    <td><a href="Stls/4_No_Sensors/SB_LGX_Lite_Body.stl">Body</a></td>
    <td>Credit: <a href="https://www.printables.com/de/model/576122-lgx-lite-stealthburner-filament-cutter">tommorox234</a></td>
  </tr>
</table>

### Supported Hotends for StealthBurner

<table>
  <tr>
    <th>Hotend</th>
    <th>STLs</th>
    <th>Credit</th>
  </tr>
  <tr>
    <td>V6-R6<br><a href="Stls/Hotends/V6_R6/">Repo</a></td>
    <td>
      <ul>
        <li>SB_V6_R6_Cutting_Printhead_Back.stl
        <li>SB_V6_R6_Cutting_Printhead_Front.stl
      </ul>
    </td>
    <td></td>
  </tr>
  <tr>
    <td>Rapido<br><a href="Stls/Hotends/Rapido/">Repo</a></td>
    <td>
      <ul>
        <li>SB_Rapido_TH_Cutting_Printhead_Rear.stl
        <li>SB_Rapido_TH_Cutting_Printhead_Front.stl
      </ul>
    </td>
    <td>
      <p>Credit: <a href="https://github.com/juliusjj25">juliusjj25</a>
    </td>
  </tr>
  <tr>
    <td>Dragon<br><a href="Stls/Hotends/Dragon/">Repo</a></td>
    <td>
      <ul>
        <li>SB_Dragon_Cutting_Printhead_Back.stl
        <li>SB_Dragon_Cutting_Printhead_Front.stl
      </ul>
    </td>
    <td></td>
  </tr>
  <tr>
    <td>Revo Voron<br><a href="Stls/Hotends/Revo/">Repo</a></td>
    <td>
      <ul>
        <li>SB_Revo_Voron_Cutting_Printhead_Back.stl
        <li>SB_Revo_Voron_Cutting_Printhead_Front.stl
      </ul>
    </td>
    <td> Credit: Russell Gower </td>
  </tr>
  <tr>
    <td>Bambu<br><a href="Stls/Hotends/Bambu/">Repo</a></td>
    <td>
      <ul>
        <li>SB_Bambu_Cutting_Printhead_Back.stl
        <li>SB_Bambu_Cutting_Printhead_Front.stl
        <li>SB_Bambu_Adaptor.stl
        <li>SB_Bambu_Adaptor_M5_Nut.stl
      </ul>
    </td>
    <td>Credit: Jakub Kadlec (Facebook)</td>
  </tr>
  <tr>
    <td>Slice Mosquito<br><a href="Stls/Hotends/Mosquito/">Repo</a></td>
    <td>
      <ul>
        <li>Slice_Mosquito_Cutting_Printhead_Front_And_Rear.stl
      </ul>
    </td>
    <td>Credit: <a href="https://www.printables.com/de/model/614813-filametrix-mod-for-slice-engingeering-mosquito-hot">MakeAUsername_285162</a></td>
  </tr>
</table>
</details>

<br>

## How it works

Proof of concept [Video 1](https://youtube.com/shorts/HOMG8cVk_U4)

Proof of concept [Video 2](https://youtu.be/tTcrxttyths)

Filametrix [in action](https://www.youtube.com/watch?v=tfMZWQRqtvY)

<br>

> [!NOTE]  
> - You will need to use one of the ADXL mounting threads
> - Careful placement of the cutting point will minimize impact (if any) to build area.  Note that a gantry servo option is available for operating the "Depressor Pin" to ensure no impact

<br>

## What you need
### Print list
#### Toolhead
- 1x SB (hotend name) Cutting Printhead Back
- 1x SB (hotend name) Cutting Printhead Front
- 1x SB Main body Cutting with ECAS (with selected sensors)
- 1x SB motor plate (as Stealthburner has seen a small update the newest plate does not fit anymore. So please use the one from this git)
- 1x SB Latch ECAS
- 1x Cutting Arm
- 1x Knife Holder

#### Cutting point on gantry
- 1x Depressor Mount
- 1x Depressor

#### Cutting point on gantry with servo
- tbd...

### Parts list - considering you already have a Stealthburner with Dragon Hotend

#### Toolhead: 
- Loctite
- 1x M3 nut (DIN934; idealy a countersunk tool to modify the nut for proper filament insertion)
- 2x M3 washer (0.5mm)
- 1x M3x18 SHCS (it repleaces the top left M3x25 SHCS from the SB-Cover mount) 
- 2x Voron heat inserts
- 1x M3x18 FHCS (counter sunk screw)
- 1x M3x8 SHCS
- 1x M2.5x16 SHCS (15-18mm works)
- Spring 0.4x4x15 or alternative of ballpoint pen (L=15mm; D<=4,5mm) (I've ordered some for testing, to have a "defined" spring)
- Type 4 metal hobby blades (we will cut it to length) [Link](https://de.aliexpress.com/item/1005005117830095.html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) Amazon link, these need glue to be held in but work fine (USA) [Link](https://www.amazon.com/dp/B07QP8L1QG)

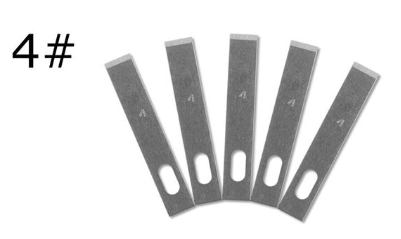
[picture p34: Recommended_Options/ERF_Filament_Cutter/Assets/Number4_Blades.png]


#### Cutting point on gantry
- 1x M3x16 BHCS
- 1x M3 nut
- 1x M3x8 FHCS
- 2x M3 SHCS (Lengths: 6mm - no backers, 10mm - titanium backers, 12mm - MGN9 rails)
- 2x Voron heat inserts

<br>
<hr>

## Assembly
### Cutting arm
<table>
  <tr>
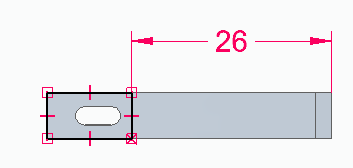
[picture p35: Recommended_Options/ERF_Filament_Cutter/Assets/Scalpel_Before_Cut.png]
Scalpel Before Cut
    <td width=40%></td>
    <td>Cut scalpel to length l=26mm</td>
  </tr>
  <tr>
    <td width=40%>Scalpel After Cut</td>
    <td>After cut</td>
  </tr>
  <tr>
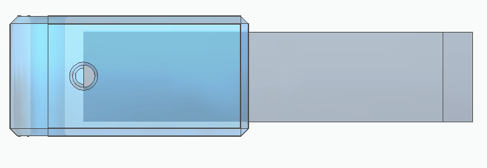
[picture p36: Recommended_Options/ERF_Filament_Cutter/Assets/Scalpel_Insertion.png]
Scalpel Insertion
    <td width=40%></td>
    <td>Insert scalpel into knife holder</td>
  </tr>
  <tr>
    <td colspan=2>Insert the scalpel (which is cut to 26mm) into the knife holder until you see it in the little hole. Use pliers to push it into the knife holder. Some force should be needed as the scalpel should stay in place due to the "pressfit". If that's not the case add some glue.(Depending on scalpel tolerances)</td>
  </tr>
  <tr>
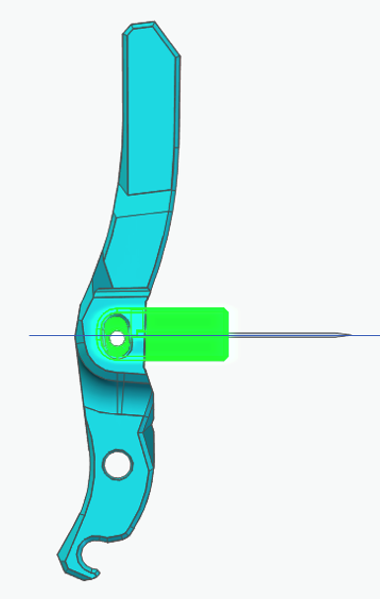
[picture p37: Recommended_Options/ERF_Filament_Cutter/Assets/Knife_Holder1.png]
Holder1
    <td width=40%></td>
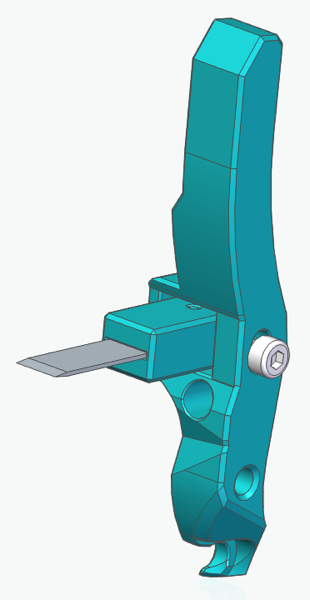
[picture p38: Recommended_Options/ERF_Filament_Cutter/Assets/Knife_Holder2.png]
Holder2
    <td></td>
  </tr>
  <tr>
    <td colspan=2>Put knife holder into cutting arm. The M2.5x15 screw is directly screwed into the plastic of the knife holder. The tip of the screw should be flush with the cutting arm or no more than 0.1-0.3mm above it. Check the orientation of the hole for the M2.5 screw in the knife holder. It needs to be on the bottom side.</td>
  </tr>
</table>

> [!NOTE]  
> The knife holder must move up and down without friction in the cutting arm but shoult not have a lot play. Maybe some grinding is needed.

### Toolhead Body
<table>
  <tr>
    <td width=40%>SB Main Body</td>
    <td>Add heat inserts. Tip here for the heat set that goes above the cutter - suggest drilling the threads out with a ~2.5mm drill bit. On the hotend holder side below the cutter make sure you flare out the PTFE tube to help guide the filament.</td>
  </tr>
  <tr>
    <td width=40%>SB Cutting Printhead</td>
    <td>SB cutting Printhead back</td>
  </tr>
  <tr>
    <td width=40%>Depressor</td>
    <td>Depressor - one on either end, end with ribs should be flush with surface below ribs with no plastic sticking up past surface</td>
  </tr>
  <tr>
    <td width=40%>Depressor</td>
    <td>Finished cutting point assembly should look like this. Note: for titanium backers, the backer should be centered between belt clamps and the end of the depressor mount should be flush with the end of the backer. This will work for all backers with 10/20/40mm spacing with the furthest back hole 5-15mm from the end. Height of depressor should be adjusted to press in the depression on the cutting arm and the BHCS can be adjusted in and out for the right positioning and locked in place with the M3 nut</td>
  </tr>
</table>

<br>

## Happy Hare Setup

### In mmu_parameters.cfg:

`form_tip_macro: _MMU_CUT_TIP` to instruct Happy Hare to use the filament cutter rather than normal tip forming.

Make sure `toolhead_extruder_to_nozzle` and `toolhead_sensor_to_nozzle` are set to your particular toolhead as per the Happy Hare documentation.

`force_form_tip_standalone: 1` this tell Happy Hare to always use the tip cutting macro.

> [!IMPORTANT]  
> Make sure you turn off tip forming or any extruder movements in your slicer - the slicer must not take any part in the filament swap. It should pick up when purging the new filament to the purge block.

### In mmu_filamentix.cfg:
Configure the `_MMU_CUT_TIP` macro variables as per the instructions in the file.

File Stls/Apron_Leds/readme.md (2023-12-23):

# Apron Neopixels

The neopixel holder is designed to snap on the 2020 extrusion just under each gate. It consists of a Holder and a cover. One of each per gate.
## what to print ?
* **2 holders are available :**
  * One for a strip of LED 10mm wide.
    * **Holder_Strip_Leds_xN.stl**
  The same is used to light the chamber of the Voron printers with a spacing of 16.5mm. It can be found on aliexpress. We used the RGBNW, 1m 60 IP30, Black PCB <br> https://fr.aliexpress.com/item/32476317187.html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
  * The second is designed to hold the individual neopixel RGBW LED.
    * Holder_PCB_Led_xN.stl
  Those are the same neopixels used in the stealthburner.
  The holders are printed standing up with an (optional) brim ears STL : Holder_Brim_ears_xN.stl<p>
* **2 versions of the covers are  provided :**
  * One that print flat but need supports (**recommended**).
    * **Cover_Body_xN.stl**
    * **[t]_Cover_Lens_xN.stl**
    
  * One that print standing up with no supports.
    * Options/Cover_Body_No_support_xN.stl
    * Options/[t]_Cover_Lens_No_support_xN.stl

The recommended STLs are :
  *  Holder_Strip_Leds_xN.stl because strip leds are much easier to solder and install.
  *  Cover with support. They give a better look especially on the lens part that can be printed with concentric(filled) top and bottom infill :
     *  **Cover_Body_xN.stl**
     *  **[t]_Cover_Lens_xN.stl**

## Tips

**Printing tips.**
* Holder can be print in any color. It is not visible.
* Cover_Bodies should be printed with opaque filament.
* Cover_lenses should be print with transparent filament.
* Load both files together into the slicer.
     Answer "Yes" to the mulicolor print dialog box.
* Select the color of your choice for the body, and transparent for the lens. 
    
* Add bottom and top infill pattern settings to the lens, and select concentric(filled) pattern. 
   
   Slice and print.
**Installation of the recommended STLs**
* Cut N individual LED form the strip, and tin all the solder pads.
* Snap all the holders on the 2020 extrusion under the filament blocks.
  * one side of the tang that snaps to the extrusion does not go up to the end. This is made to accommodate for the roll in nuts.
  * If for some reason you have a roll in nuts on both side of the holder, the opposite site can be cut off. 
* Stick each individual strip in the holder.
* Solder thin rigid wires between the strips.
* On gate 0 solder 3 wire that will go the RGB pin of the controller.
  * a small opening on each corner of the holders is used to pass the wires through.
  * At the last gate you can also solder 3 wires if you plan to add more RGB LEDs.
  * Snap the covers on the holders.

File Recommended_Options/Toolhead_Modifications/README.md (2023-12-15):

# Enraged Rabbit toolhead filament detection

This page explores the various options available for Toolhead Filament detection that is used by your MMU firmware to ensure reliable filament loading and to spot errors that might occur during the filament's loading and unloading processes. The ERCFv2 team advocate the utilization of a toolhead sensor only or dual-sensor system. In this section, you will find a comprehensive collection of standalone sensor options compatible with popular toolheads.

> [!IMPORTANT]  
> **Secured bowden**: It is important to ensure the bowden tube can't accidently separate from either the MMU or the toolhead. This is essential when opting for no toolhead sensors. We recommend secure fastening using a Push-Fit or ECAS connection. We wish to highlight that there are certain toolheads, such as the stock CW2, where the Bowden tube is simply inserted without any additional securing mechanism. Such setups present a heightened risk of the bowden tube dislodging from its holder and thus we offer a no-sensor version of these toolheads.

> [!NOTE]  
> **Using a filament cutter toolhead**: For users who have integrated the ERF filament cutter into their systems, please refer to the toolhead modifications outlined in then [ERF Filament Cutter](../ERF_Filament_Cutter/README.md) section where you will find a similar set of toolhead modifications but including the cutting option.

<br>

_____________________________

## Possible Options Explained
Position of the sensor
<p><em>Position of the sensor</em></p>

### **1. Toolhead and Entry Sensor**  
This setup allows the firmware (Happy Hare) to quickly load bowden and optionally home prior to extruder, then home to toolhead sensor before loading to the nozzle. The entry sensor also allow for easier calibration of the bowden length.  The twin sensors also allows for precise location of the filament in an error situation which increases the chances of automatic recovery. The downside is that you need two switch inputs to your MCU. **This is the luxury option.**  
   
✔ smooth bowden loading<br>
✔ precise extruder loading<br>
✔✔ great error recovery (excellent through precise filament location)

### **2. Toolhead Sensor only**  
With this setup the firmware can quickly load close to the nozzle and then precisely home to the toolhead sensor inside the extruder. The presence of the toolhead sensor is highly valuable in a MMU so the firmware allowing detection of correct behavior, smooth loading and auto recovery. This is usually an easy setup to accomodate and many toolhead boards or MCUs provide for this input. This option has a small possibliy of the filament not being detected as trapped between extruder and sensor but this is rarely a problem in practive. **This is the most common recommended option.**  
  
✔ smooth bowden loading<br>
✔ precise extruder loading<br>
✔ good error recovery (with in-extruder detection)

### **3. Entry Sensor only**  
With this setup the firmware can quickly load the bowden and home to a point close to the nozzle. Because the filament has not yet passed into the extruder there are inaccuracies that can occur during this transistion. Also this option has no way of knowing the filament is inside the extruder in error recovery situations and thus relies on additional user interaction.
     
✔ smooth bowden loading<br>
✘ extruder loading can be inprecise<br>
✘ poor error recovery (no way to determine if filament is inside extruder)

### **4. No Sensor**  
This setup has no sensors and is thus not recommended but it can be used if you have not other options with Happy Hare. It does include a secure bowden connection (ECAS or push fit) which is essential because the filament will be colliding with the extruder entrance. **This works but is not recommended.**  
  
✘ rough bowden loading that can fail (this system relies on collision detection when the filament hits the extruder)<br>
✔ extruder loading precision is reasonable<br>
✘ poor error recovery (there is no way to assertain the filament position)
_____________________________
 
## Recommend Mods
Here are the STLs for popular Toolhead/Extruder combinations.  Note that this is a compiled list and we invite you to help flesh out the rest...

<details open>
<summary><strong>Expand for Stealthburner Options</strong></summary>
<table>
  <tr>
    <th>Extruder</th>
    <th>1. Toolhead &amp; Entry Sensor</th>
    <th>2. Toolhead Sensor</th>
    <th>3. Entry Sensor</th>
    <th>4. No Sensor</th>
  </tr>
  <tr>
    <td>Clockwork 2</td>
    <td> <a href="./Stls/1_Toolhead_And_Entry_Sensors/[a]_SB_CW2_Latch.stl">Latch</a> <br> <a href="./Stls/1_Toolhead_And_Entry_Sensors/SB_CW2_Body.stl">Body</a> <br> <a href="./Stls/1_Toolhead_And_Entry_Sensors/SB_CW2_Plate.stl">Plate</a> <br> <sub>Additional items: <br> 1x ECAS <br> 2x D2F-5 <br>2x ball 5,5mm <br> 4x self tapping screw M2x10 <br> Credit: <a href="https://www.printables.com/model/466692-stealthburner-cw2-filament-sensors-with-ecas-latch">Petr Kašpar</a></sub> </td>
    <td> <br> <sub>Additional items: <br> 1x ECAS <br> 1x D2F-5 <br>1x ball 5,5mm <br> 2x self tapping screw M2x10</sub> </td>
    <td> <br> <sub>Additional items: <br> 1x ECAS <br> 2x D2F-5 <br>2x ball 5,5mm <br> 4x self tapping screw M2x10</sub> </td>
    <td> <a href="./Stls/4_No_Sensors/SB_CW2_Latch.stl">Latch</a> <br> <a href="./Stls/4_No_Sensors/SB_CW2_Body.stl">Body</a> <br> <sub>Additional items: <br> 1x ECAS</sub> </td>
  </tr>
  <tr>
    <td>Orbiter 2</td>
    <td></td>
    <td></td>
    <td></td>
    <td></td>
  </tr>
  <tr>
    <td>LGX Lite</td>
    <td></td>
    <td></td>
    <td></td>
    <td></td>
  </tr>
  <tr>
    <td>Galileo 2</td>
    <td></td>
    <td></td>
    <td></td>
    <td></td>
  </tr>
  <tr>
    <td>other extruder</td>
    <td></td>
    <td></td>
    <td></td>
    <td></td>
  </tr>
</table>
</details>

<details>
<summary><strong>Expand for XOL2 Options</strong></summary>
<table>
  <tr>
    <th>Extruder</th>
    <th>1. Toolhead &amp; Entry Sensor</th>
    <th>2. Toolhead Sensor</th>
    <th>3. Entry Sensor</th>
    <th>4. No Sensor</th>
  </tr>
  <tr>
    <td>Clockwork 2</td>
    <td></td>
    <td></td>
    <td></td>
    <td></td>
  </tr>
  <tr>
    <td>Orbiter 2</td>
    <td></td>
    <td></td>
    <td></td>
    <td></td>
  </tr>
  <tr>
    <td>LGX Lite</td>
    <td></td>
    <td></td>
    <td></td>
    <td></td>
  </tr>
  <tr>
    <td>Galileo 2</td>
    <td></td>
    <td></td>
    <td></td>
    <td></td>
  </tr>
  <tr>
    <td>other extruder</td>
    <td></td>
    <td></td>
    <td></td>
    <td></td>
  </tr>
</table>

</details>
<details>
<summary><strong>Expand for other toolhead options</strong></summary>
<table>
  <tr>
    <th>Extruder</th>
    <th>1. Toolhead &amp; Entry Sensor</th>
    <th>2. Toolhead Sensor</th>
    <th>3. Entry Sensor</th>
    <th>4. No Sensor</th>
  </tr>
  <tr>
    <td>Clockwork 2</td>
    <td></td>
    <td></td>
    <td></td>
    <td></td>
  </tr>
  <tr>
    <td>Orbiter 2</td>
    <td></td>
    <td></td>
    <td></td>
    <td></td>
  </tr>
  <tr>
    <td>LGX Lite</td>
    <td></td>
    <td></td>
    <td></td>
    <td></td>
  </tr>
  <tr>
    <td>Galileo 2</td>
    <td></td>
    <td></td>
    <td></td>
    <td></td>
  </tr>
  <tr>
    <td>other extruder</td>
    <td></td>
    <td></td>
    <td></td>
    <td></td>
  </tr>
</table>
</details>

_____________________________

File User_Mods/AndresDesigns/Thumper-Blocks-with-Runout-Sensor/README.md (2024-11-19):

# Thumper Block with integrated Runout Sensor

This mod adds support for filament presence detection using a D2F-style switch. The author doesn't use GitHub so you can find the project here: https://www.printables.com/model/1053193-thumper-block-with-integrated-runoutsensor

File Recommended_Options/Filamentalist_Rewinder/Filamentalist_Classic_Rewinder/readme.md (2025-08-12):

<p align="center">
<h1 align="center">The Filamentalist "Classic" Passive Filament Driven Rewinder</h1>

<p align="center">]
</p>
   
## [Filamentalist Classic Assembly Guide Document](https://github.com/Enraged-Rabbit-Community/ERCF_v2/blob/a68bc6678bab41d7bded5e42a17276a9430a0f45/Recommended_Options/Filamentalist_Rewinder/Filamentalist_Classic/Do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)  [](https://github.com/Enraged-Rabbit-Community/ERCF_v2/blob/a68bc6678bab41d7bded5e42a17276a9430a0f45/Recommended_Options/Filamentalist_Rewinder/Filamentalist_Classic/Do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)

## [Filamentalist Classic Assembly Guide Video](https://youtu.be/-1cHOcnosxE?si=RZV318OI9f3f_CkE)  [](https://youtu.be/-1cHOcnosxE?si=RZV318OI9f3f_CkE)

##  **BOM:**

**ATTENTION!! PLEASE READ COMMENTS IN FAR RIGHT COLUMN** (you may need to scroll over in your view)

| Qty per Site | Part | Example Source Reference | Comments |
|---|---|---|---|
| 1 | 8mm dia. x 80mm Stainless Steel Dowell Pin | https://www.amazon.com/uxcell-Stainless-Chamfered-Support-Elements/dp/B0BC8VFSWD, Amazon Alternate https://www.amazon.com/Unifizz-Stainless-Steel-Round-Silver/dp/B09P9MC953?th=1 (sheared ends may need to be cleaned up), Aliexpress https://www.aliexpress.us/item/3256801518620991.html | Undersized shaft (7.93-7.97mm or 5/16" dia) works the best.  100mm length is more available and can extend out of rewinder, you can cut polished 8mm or 5/16" diameter stainless rod to length, or there are stls to make a wider rewinder based on a 100mm axle.  Custom rewinder widths are also possible using the Fusion 360 parametric model and you can cut shaft to whatever length is desired. 8mm (or 5/16") diameter straight stainless tube is also an excellent alternative to solid rods as the are much easier to cut to length. |
| 5 | MR608 bearings | Can be obtained anywhere (Home Depot, Amazon, Aliexpress, etc.)  | MR608-2RS style recommended, but open or  MR608-ZZ style will work |
| 1 | HF081412 One-Way Bearing | https://www.amazon.com/dp/B0C7TRFJBS, Aliexpress | 8mm Bore, 12mm length, 14.2mm Diameter. Get the "octogonal" style. |
| 1 | ECAS press-in pneumatic fittings for the bowden tubes (like used in ERCF)  |  | A locking clip is required and can be bought or printed (stl included).  The rubber seal is not needed and should not be installed upon assembly. |
| 2 | O-rings | Metric 3.5x20 (ID) or AS568 Standard size 211, Home Depot #110, Amazon example: https://www.amazon.com/211-Buna-N-Ring-Durometer-Black/dp/B000FN0W7I/, Aliexpress example: https://www.aliexpress.us/item/2255799953260685.html (select correct size) | In the range of 13/16" ID, 1-1/16" OD or ~20mm ID, ~27mm OD, ~3.5mm cross section/cs, Nitrile Butadiene Rubber (NBR or Buna-N)|
| 1 | Spring  | https://www.amazon.com/dp/B076LNJF5Q, Aliexpress | Like in extruders - 304 Stainless Steel,6mm OD,0.6mm Wire Size,7.5mm Compressed Length,15mm Free Length (the stiffer 1mm wire size extruder spring used on CW2 and G2E will also work if you have those on-hand) | |
| 1 | 3mm Heatset Insert | M3x4x5 like these:  https://www.amazon.com/gp/product/B09MCW7ZN5 | Voron standard size | set into the Tensioner Mnt |
| 1 | 3x35mm SHCS | SS Socket Head Cap Screw | Spring Tensioner Screw anything in the range of 35mm +/- 10mm should work.  If building the alernate reverse access version then a 30mm length is recommended. |
|  2-6  | M3x8 SHCS  |  Stainless Steel Socket Head Screw | for locking rim rollers to 8mm steel axle shaft.  1 to 3 screws per roller Depending on tightness/looseness of Rim Roller center bore |
| 6 | 3x12 FHCS  |  Stainless Steel Flat Head Screw | for Tensioner Mnt and Rear Axle installation 8/10/12mm lengths will work|
| 3 | 3x18 FHCS  |  Stainless Steel Flat Head Screw | for Tensioner Arm clamp bearings and Tensioner Mnt pivot installation 16mm length will work |
| 1 | M3 Washer  |  Stainless Steel | between Spring Tensioner screw head and spring |
| 4 | Rubber Band | See [FAQ](https://github.com/Enraged-Rabbit-Community/ERCF_v2/blob/master/Recommended_Options/Filamentalist_Rewinder/Filamentalist_FAQ.md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)) | bike tire inner tube or rubber bands |

**Optional Parts**
| Qty per Site | Part | Example Source Reference | Comments |
|---|---|---|---|
| 1 | D2F-L3 Microswitch  | Omron brand - Mouser, Digikey, etc., Aliexpress example: https://www.aliexpress.us/item/3256805036222979.html  | for pre-gate sensor option versions |
| 2 | M2x10 Self Tapping Screw | Philips or socket head.  Amazon example: https://www.amazon.com/DTGN-M2x10mm-Phillips-Self-tapping-Screw/dp/B0CSRTYBLR, Aliexpress example: https://www.aliexpress.us/item/3256802486141312.html (select size) | for pre-gate sensor option versions |
| 1 | JST-XH 2-pin Socket/Plug | Amazon example:  https://www.amazon.com/CQRobot-Connector-Terminals-Housing-Adapter/dp/B0B2R966ZY, Aliexpress Example: https://www.aliexpress.us/item/3256804799083128.html (need housing, plug, and terminal) | for pre-gate sensor option versions |
| var. | 24 awg wire  | | for pre-gate sensor option versions |
| var.  | 2.5mm ID PTFE tubing | Amazon, Aliexpress, 3D printing vendors | 2.5mm ID recommended but you can try whatever you have.  Length depends on the distance from your rewinder location to your ERCF inputs |

##  Printing Guidelines:

## **General:**
- Material: ABS or ASA (~170 gm per site)
- Print Time: ~8hr 17min (based on the Ellis PIF profile speeds, accelerations, and volumes)
- 0.2mm layer height
- 40% infill recommended.  Linear style infills are fastest (rectilinear, monotonic, grid, triangles, stars, etc.)
- Wall Count: 4
- Solid Top/Bottom Layers: 5

## **Part Specific:**
- Orientation suggestions are relative to the installed assembly orientation and are shown in the slicer images below.
- There are stls for both 80mm and 100mm wide version and a Fusion 360 parametric CAD model for additional custom widths.  See "Additional Notes/Considerations" point 3 above for more details.
- If rotating the Filamentalist is not feasible for your required filament loading direction or you need a bottom feed capability (for example enclosure limitations or feeding through the bottom of a shelf) there is an option for a rear loading version which only requires printing the Tensioner_Mount_Rear_Load_80mm/100mm_[option] in the place of Tensioner_Mount_80mm/100mm part.
  
  

- Stl's are provided for optional clip-in style supports where no Base_Plate is needed and the rewinders are easily clipped in and out of (2) 2020 extrusions mounted 170mm center-to-center apart.  This option is highly recommeded if your setup can accomodate this style type of mount.
  
  
- **!! IMPORTANT !!  This design relies on multiple press-fits for bearings and ECAS fittings.  As a result, printer calibration is important.  A Test_Block stl is included.  It is highly recommended that you print this block first, check fits, and make adjustments to extrusion multipliers and/or slicer scaling if needed before printing the Filamentalist parts.**
  
    

| **Qty per Site** | **Part**  | **Pic** |  **Orientation** | **Printed Supports Needed** | **Comments** |
|---|---|---|---|-----|---|
| 1 | Right_Support |  |  Horizontal | N | |
| 1 | Left_Support |  | Horizontal | N | |
| 1 | Option: Right_Support_[2020_Clip-In_option] |  |  Horizontal | N | |
| 1 | Option: Left_Support_[2020_Clip-In_option] |  | Horizontal | N | |
| 1 | Base_Plate_80mm/100mm_[option] |  | Horizontal | N | Optional part for a standalone unit not mounted to another surface  |
| 1 | Idler_Roller_Axle_80mm/100mm  |  | Horizontal | N | align flat of "D" to build plate |
| 2 | [a]_Rim_Roller_80mm/100mm |  | Horizontal | N | Dished side up. |
| 1 | [a]_Center_Drive_Roller  |  | Horizontal | N | Recommend scattered seams for press fit-bore concentricity |
| 2 | CDR_Spacer_80mm/100mm |   | Horizontal | N | |
| 1 | Tensioner_Arm_Left |   | Horizontal |  N |  |
| 1 | Tensioner_Arm_Right |   | Horizontal |  Built-in | Remove built-in support from the locking tab |
| 1 | [a]_Tensioner_Mount_80mm/100mm |  | Vertical (as installed) | N  | There is a pre-gate sensor option version available as well (split to parts in slicer for print-in-place breakaway connector retaining key).  |
| 1 | [a]_Tensioner_Mount_Rear_Load_80mm/100mm _[option] |  | Vertical (as installed).  Optional for rear loading if needed. | N  | There is a pre-gate sensor option version available as well.  |
| 1 | [a]_Idler_Roller _(male) _80mm/100mm |   | Vertical  | N  |  Scattered seams |
| 1 | [a]_Idler_Roller _(female)_80mm/100mm |   | Vertical  | N  |  Scattered seams |
| 1 | Axle_Depth_Tool_80mm/100mm |  | Vertical | N | Pocket opening up.  Print with 100% infill for reuse strength and durability when building multiple rewinders. |
| 2 | [a]_ECAS_Clip |  |  Horizontal | N | Tab up |
| 1 | Test_Block |  |  608 Pocket facing up | N | printer calibration tool |

##  Tuning

Tune by setting the Tensioner Arm clamping force.  The arm does not need an extreme amount of tension.  To tune the spring force, lift the tensioner and insert a section of filament through the o-ring bearing interface and into the bowden tube.  Hold the center roller by placing your thumb against the o-rings and try to pull the filament out.  You want the slip force to be slightly more than what the overall system drag is, so you have to imagine the range of gear motor pull force vs rewinder drag and set a slip range in-between the two "imaginary" lines.  Adjust the spring tensioner screw accordingly and err on the light side.  Run the rewinder (see test code below). If loose filament is forming around the filament spool during unload, tighten the spring tensioning screw.  If no loose filament is forming around the filament roll, gradually reduce the spring tension until loose filament starts to accumulate and then increase tension in ~1/2 screw turn increments until you feel you have the lightest tension that results in a tightly packed unload. 

##  O-Ring Replacement

You may never need to replace o-rings.  Testing and extrapolation estimates that the wear-out point is ~5K cycles.  The impact of o-ring wear-out can be reduced by periodically swapping highly used rewinders with low use rewinders in your line-up.  Also, o-rings with grooves worn in them can be swapped with their opposing partners to present the unworn side/face to the filament to extend the life of a set.  For o-ring replacement, remove the Drive Roller Assembly from the rewinder (unscrew the (6) screws of the Right and Left Supports).  Then unscrew the set screw on one Rim Roller.  You can now slide the CDR Spacer and Center Drive Roller from the axle, remove the old o-rings (a dental pic works great), and install a pair of new ones.  Reinstall the Center Drive Roller and CDR Spacer back on the axle and install the Rim Roller back onto the axle per 3.3 above, and re-install the supports.  

##  Troubleshooting

Please see [troubleshooting guide](troubleshoot.md), reference the [FAQ](Filamentalist_FAQ.md), or join our discord server (https://discord.gg/uDcGxukRKd) for more help.

#  Version History

Versioning convention.  V"X"."Y"."Z"
- "X" represents a major change in form, fit, or function.  An increment in "X" may not require that existing built units undergo rework but the new parts will generally not be compatible with past version rewinders.
- "Y" represents a "step rev" or minor revision.  These are generally small "tweaks" for improved functionality, useability, and/or assembly and typically would not require reprint/rework for existing rewinders.  
- "Z" represents a backwards compatible "bug fix".  This will generally be addressing nuisance CAD or printability issues.

V1 - 5/17/24 - Public release into ERCF V2 RC2 repository

V1.1 - 5/19/24 - Update to CAD and stls for Tensioner Arms to remove potential filament catching point during endless spool ejection

V1.2 - 5/20/24 - Reverted Center_Drive_Roller to cylindrical press fit hole (vs hex of V1 and V1.1).  Revised 608 press fit pockets of Idler_Roller_(male&female) parts for both 80mm and 100mm width versions for improved press fit.

V1.3 - 5/20/24 - Added bevel to internal step on  Idler_Roller_(male) part for 80mm and 100mm versions to improve printability.  Updated the .f3dparametric file, step files, and stls for 80mm and 100mm versions.

V1.4 - 5/21/24 - Shortened threads on Idler_Roller_male parts by 1.5mm to remove slight interference.  Updated CAD, 80mm, and 100mm stls.

V1.5 - 6/4/24 - Slightly deepened 608 bearing pockets in Idler Roller parts to prevent potential side loading binding due to print/assembly tolerances.  Reprint not required for existing functioning units.

V1.6 - 6/12/24 - No mandatory reprints/rebuilds required:  Updated CAD parametric model and 80/100mm step files because two  Tensioner Mount-to-Support holes were getting "buried" in the 100mm version.  Updated the Tensioner_Mount_100mm stl file as well.

V1.7 - 6/13/24 - Opened up c-sunk hole on Tensioner_Arm_Left part pivot screw hole to allow for full seating of a FHCS head and use of a 16mm long screw.  A new stl for Tensioner_Arm_Left ans new f3d and step files are included.

V1.8 - 7/2/24 - Removed notch/gap in axle pressing tool that shouldn't have been there.  80/100mm stl's updated as well as f3d and stp CAD files.

V2 - 7/22/24
  1. Added Rear Load option Tensioner_Mount (works as bottom load too)
  2. Removed threaded Rim Roller option and converted Rim Rollers from press-fit to set screw style.
  3. Add 608 bearing inner race clearance back into Supports.
  4. Added ~2mm of additional bowden capture in Tensioner_Mounts

V3 - 8/5/24
  1.  Add options for Tensioner Mounts with pre-Gate sensors
  2.  Included option for the Filamentalist Enclosure style Base Supports
  3.  Updated all supports to include a spool guide rail to help keep spools from wandering off of the rollers.

V3.0.1 - 8/8/24 - No reprint/rebuild required:
1. Improved clearances for indexing tab feature in Tensioner Arm parts
2. Improved breakaway feature for small print-in support in Tensioner_Arm_Right part 
3. Provided additional edge chamfering to Idler Roller Axles
4. Reinstated design history in Filamentalist_(parametric)_V3.f3d CAD model so that the parametric functionality would work correctly.
5. Added accent color to file naming convention in stl file names.
6. Updated pdf manual to reflect/describe accent color for file naming convention in stl file names.

V3.0.2 - 8/15/24 - No reprint/rebuild required:
1. Added more reference dimensions to the User Parameters section for the Filamentalist_(parametric).f3d parametric CAD model.

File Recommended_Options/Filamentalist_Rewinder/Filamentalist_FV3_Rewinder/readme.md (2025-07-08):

<p align="center">
<h1 align="center">The Filamentalist V3 ("FV3") Passive Filament Driven Rewinder</h1>
<p align="center">

</p>

## [FV3 Assembly Guide Document](https://github.com/Enraged-Rabbit-Community/ERCF_v2/blob/master/Recommended_Options/Filamentalist_Rewinder/Filamentalist_FV3_Rewinder/Documentation/Filamentalist_V3_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)  [](https://github.com/Enraged-Rabbit-Community/ERCF_v2/blob/master/Recommended_Options/Filamentalist_Rewinder/Filamentalist_FV3_Rewinder/Documentation/Filamentalist_V3_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)
##  **BOM:**

**ATTENTION!! PLEASE READ COMMENTS IN FAR RIGHT COLUMN** (you may need to scroll over in your view)

| Qty per Site | Part | Example Source Reference | Comments |
|---|---|---|---|
| 1 | 8mm dia. x ##mm Stainless Steel Rod, Tube, or Dowell Pin | https://www.amazon.com/uxcell-Stainless-Chamfered-Support-Elements/dp/B0BC8T7ZQB?th=1, Aliexpress https://www.aliexpress.us/item/2255800287548941.html (select M8x70mm) | Undersized shaft (7.93-7.97mm or 5/16" dia) works the best.  50mm axles will work in the standard width design but longer axles cut to length (up to ~75mm) will provide greater stability for the Rim Rollers.  The Classic Filamentalist 80mm axles will work but hang over ~1mm per side.  Custom rewinder widths are possible using the Fusion 360 parametric model and you can cut shaft to whatever length is desired.  8mm (or 5/16") diameter straight stainless tube is also an excellent alternative to solid rods as they are much easier to cut to length like https://www.amazon.com/uxcell-Stainless-Thickness-Seamless-Straight/dp/B081GBTQGC or https://www.aliexpress.us/item/3256805495613016.html. |
| 1 | 688 bearing | For Tensioner Arm|
| 4 | 608 bearings | For Drive and Idler axles.  Can be obtained anywhere (Home Depot, Amazon, Aliexpress, etc.)  | Inexpensive MR608-2RS rubber dust seal style is recommended as they are slightly higher resistance than the open or ZZ metal seal style. You actually want a little of resistance in the axle bearings to help the 1-way bearing unlock. |
   OR:
|   4   | 688 bearings | As an alternative to the 608 bearings for Drive and Idler axles, so would be a total of 5 688 bearings including the Tensioner Arm bearing.  This allows for only needing to buy one bearing size but the 688's might be a tighter fit on the axle shafts.  Inexpensive MR688-2RS rubber dust seal style is recommended as they are slightly higher resistance than the open or ZZ metal seal style. You actually want a little of resistance in the axle bearings to help the 1-way bearing unlock. |
|   1   | HF081412 One-Way Bearing | https://www.amazon.com/dp/B0C7TRFJBS, Aliexpress | 8mm Bore, 12mm length, 14.2mm Diameter. Get the "octogonal" style. |
|   1   | ECAS04   |  | Press-in pneumatic fitting for the bowden tubes (like used in ERCF).  A locking clip is required and can be bought or printed (stl included).  The rubber seal is not needed and should not be installed upon assembly. |
|   2   | O-ring | Metric 3.5x20 (ID) or AS568 Standard size 211, Home Depot #110, Amazon example: https://www.amazon.com/211-Buna-N-Ring-Durometer-Black/dp/B000FN0W7I/, Aliexpress example: https://www.aliexpress.us/item/2255799953260685.html (select correct size) | In the range of 13/16" ID, 1-1/16" OD or ~20mm ID, ~27mm OD, ~3.5mm cross section/cs, Nitrile Butadiene Rubber (NBR or Buna-N)|
|   1   | Spring  |  https:https://www.amazon.com/dp/B076LNJF5Q, Aliexpress https://www.aliexpress.us/item/3256805126192641.html (select size per comments) | 304 Stainless Steel,6mm OD,0.6mm Wire Size,7.5mm Compressed Length,15mm Free Length |                                 |
|   1 | 3mm Heatset Insert | M3x4x5 like these:  https://www.amazon.com/gp/product/B09MCW7ZN5 | Voron standard size | set into the Tensioner Mnt |
|   1   | M3x30mm SHCS | SS Socket Head Cap Screw | Spring Tensioner Screw |
|  6-10  | M3x12-16mm SHCS  |  12-16mm length will work | for locking rim rollers to 8mm steel axle shaft.  1 to 3 screws per roller Depending on tightness/looseness of Rim Roller center bore.  4 additional screws if using the Filamentalist Enclosure Mounts |
|  4  | M3x12 FHCS  |  Flat Head Cap Screw | for Idler Roller wheels, Tensioner Bearing axle, and Tensioner Pivot |
|   12-14   | M3x8mm FHCS  |  Stainless Steel Flat Head Cap Screw | Qty 12 for 2020 center mount, 14 for Enclosure mount |
|   1   | M3 Washer  |  Stainless Steel | for Spring Tensioner screw |
|   4   | #84 Rubber Band | See [FAQ](https://github.com/Enraged-Rabbit-Community/ERCF_v2/blob/master/Recommended_Options/Filamentalist_Rewinder/Filamentalist_FAQ.md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) | 2" bike tire inner tube cut to width or rubber bands |

**Parts for Microswitch Option**
| Qty per Site | Part | Example Source Reference | Comments |
|---|---|---|---|
| 1 | Omron D2F-01FL-D3 Lever Microswitch | https://www.mouser.com/ProductDetail/Omron-Electronics/D2F-01FL-D3?qs=i1w9Bv2NFd2YXdp4zNwbgA%3D%3D  | For pre-gate sensor levered switch option. |
   OR:
|   1   | Omron D2F-01F-D3 Button Microswitch | https://www.mouser.com/ProductDetail/Omron-Electronics/D2F-01F-D3?qs=i1w9Bv2NFd2sPdBLm34BPQ%3D%3D  | For pre-gate sensor printed lever switch option. |
|   1   | MR85 Bearing | Amazon: https://www.amazon.com/dp/B07CKL54RS, Aliexpress: https://www.aliexpress.us/item/3256807026256776.html   | ZZ, RS, or open style will work.  For pre-gate sensor switch option. |
   OR:
|   1   | 8x3 Disc Magnet | Amazon: https://www.amazon.com/FINDMAG-Magnetic-Whiteboard-Refrigerator-Magnets-8x3mm/dp/B0863BGG6H, Aliexpress: https://www.aliexpress.us/item/3256806495856656.html   | For pre-gate sensor switch option. |
   OR:
|   1   | 6x3 Disc Magnet | Amazon: https://www.amazon.com/TRYMAG-Magnets-Refrigerator-Whiteboard-Neodymium/dp/B09QHSB2XM, Aliexpress: https://www.aliexpress.us/item/3256807048616464.html   | For pre-gate sensor switch option. |  
|   var.   | 24 awg wire  |   | for pre-gate sensor option versions |
|   2   | M2x8mm SHCS |  Amazon:  https://www.amazon.com/Alloy-Steel-Socket-Screws-Black/dp/B015A37DVU, Aliexpress:  https://www.aliexpress.us/item/3256806889548681.html | Self tapping screws can be used as an alternative |
| 2  | Male/Female connectors |  | Connectors of your choice, JST-XH 2-pin works well |

##  Printing Guidelines:

## **General:**
- Material: ABS or ASA (2020 Center Mount version: ~154gm per unit, Filamentalist Enclsoure Mount Version: ~175gm per unit)
- Print Time: 2020 Center Mount version: ~7hr 34min, Filamentalist Enclsoure Mount Version: ~9hr 10min (based on the Ellis PIF profile speeds, accelerations, and volumes)
- 0.2mm layer height
- 40% infill recommended.  Linear style infills are fastest (rectilinear, monotonic, grid, triangles, stars, etc.)
- Wall Count: 4
- Solid Top/Bottom Layers: 5

- Recommended orientation is set in the stl files and should load correctly into slicer programs.  Print orientation is shown below in the slicer plate pictures for base and accent color parts.
- Where applicable, stl's are provided for two different axle bearing types, 688 (16mm OD) and 608 (22mm OD) bearings.  Bearing size is denoted in the file naming.
- **!! IMPORTANT !!  This design relies on multiple press-fits for bearings and ECAS fittings.  As a result, printer calibration is important.  The Print_Calibration_Tool_###_Bearing.stl file is included.  It is highly recommended that you print this part first, check fits, and make adjustments to extrusion multipliers and/or slicer scaling if needed before printing the Filamentalist parts.**
   - Other materials such as PETG or PLA may work fine but parts were not designed or validated for these materials.  If you want to use a different material start with the Print Calibration Tool and adjust extrusion rates and slicer scaling to achieve the correct dimensions for the press fit parts.



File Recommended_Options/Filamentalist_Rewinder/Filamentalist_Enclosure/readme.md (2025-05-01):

# The "Filamentalist" Enclosure # 

The Filamentalist Enclosure is a passive dry box designed to house the Filamentalist passive rewinder.  It  consists of (4) printed endcaps, (6) pieces of 2020 extrusion cut/ordered to the desired length, and 0.060" (1/16') polycarbonate sheet(s) cut to size. Enclosure specific Filamentalist supports are required (these are included in the Filamentalist optional stl's as well as under the Enclosure stl directory).


</p>


</p>


</p>


</p>


</p>


</p>

BOM:

- 2020 Extrusion - Qty 6 - Select/cut length to be greater than or equal to [Rewinder Qty] X [Rewinder Width] + 10mm
    - for example: 6 X 81.5 (std. Filamentalist Width) + 10 = 499mm.  Round up to a standard 500mm long 2020 extrusion
    - get extrusions with holes that can be tapped to a 5mm thread (like the Misumi with a 4.2mm D hole)
    - examples: https://www.amazon.com/dp/B09DYMCBYF, https://www.aliexpress.us/item/3256801651139612.html

- Polycarbonate Sheet (Lexan) - 1/16" (also 0.060" or 1.5mm) thick.  Width of pieces = Extrusion Length -2mm (i.e. cut sheet to 498mm wide if using 500mm extrusions)
    - Lid Length = 451.5mm
    - Base Rear Panel Height = 120mm
    - Base Front Panel Height = 45mm
    - Bottom Panel Length (if used) = 230mm
    - For enclosures up to 607.6mm wide a single 24" x 36" sheet is enough material.
      - (2) 24" x 24" or (1) 24" x 24" + (2) 12" x 24" sheets will work as well if it is easier for you to source smaller sheets.
    - Sourcing Alternatives:
      - If there are difficulties sourcing the recommended Polycarbonate (Lexan) sheet material, PET and PET-G sheet has been used successfully although it wil be less scratch resistant
      - 2mm sheet can also be substituted but it will be more difficult when bending the lid panel into the lid frame and end caps

- Seal Material - ~10m or 32ft of 3/8" wide x 1/4" high (9mm x 6mm) self-adhesive weather seal.  Something like this:  https://www.homedepot.com/p/M-D-Building-Products-17-ft-Black-Small-Rubber-Auto-Marine-Weatherseal-for-All-Climates-01025/202066509, or https://www.amazon.com/Insulation-Weatherproof-Soundproofing-Self-Adhesive-Weatherstrip/dp/B082HDZ1P1?th=1, or https://www.aliexpress.us/item/3256806396445681.html.  Most of the glue needs to be peeled off so you want the style that has the "strings" embedded in the glue to aid in removal.

- M5x10/12mm length BHCS or SHCS - Qty 6 - For securing end caps to extrusions.  BHCS (Button Head) looks the best.

- M5 10mm length BHCS - Qty 4 - for mounting hinges to base and lid frames

- M5 x 16/18/20mm length BHCS - Qty 2 - Hinge Pin Screws.

- M3 x 4/5mm length BHCS or SHCS - Qty 2 - for tying lid panel to lid endcaps.

- 5mm Heatset Insert - Qty 2 - Optional, for setting how far the lid hinges back.

- M5 x 8/10mm length SHCS - Qty 2 - Optional, for setting how far the lid hinges back.
  
- 6mm OD/4mm ID grommets for sealing  bowden tubes. Drill 6.5mm holes.  Example:  https://a.co/d/bBc6JAL

(6) standard width (81.5mm) Filamentalist will fit in the 500mm length extrusion version of the enclosure.  There is room, and some special "far left" and "far right" extended supports that allow you to build one ~94mm wide Filamentalist unit using the parametric model to support a wider spool like KVP or NinjaFlex.

**Assembly Tips:**

**Lid Panel Installation:** The 0.060" Lexan bends easily but it is not easy to bend it and get it captured in the lid endcaps and extrusions.  Its a two person job. If doing it alone use 2 or 3 loops of string, or even better adjustable straps, set at a length to hold the correct bend and spacing at the edges of the Lexan.  Secure the non-captured end of the extrusions with a loop or strip of tape so that you don't spread/overflex the extrusions and potentially crack the endcap while installing the curved Lexan.

**Seal Installation:**


</p>

</p>

</p>

</p>

</p>

**Securing/Sealing on Printer:**

For a Voron enclosure you can "straddle" the top panel like the pic below.  Drill 2 countersunk holes in the top panel and screw them into t-nuts in the bottom enclosure extrusion.  The screw heads sit just below the panel surface so that the bowden tube doesnt catch on them while the print head is zooming around.   Run seal material in the rear bottom extrusion channel of the enclosure. Cut out sections of the weather stripping base to make space for the t-nuts to sit under but leave a continuous piece of weatherstripping seal running over the top of the t-nuts.  You can stick toothpicks into the t-nut holes (or 3mm screws with the heads cut off) to serve as locating pegs when you drop the enclosure onto the printer to make sure the top panel holes align with the t-nut locations.  This will pull  the top panel against the seal and is enough to secure the enclosure in place on the printer.



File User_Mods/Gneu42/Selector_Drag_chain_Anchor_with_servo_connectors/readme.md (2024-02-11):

<h1 align="center"><ins>Drag chain anchor with 2 servo connectors and spacer with tie-warp possibility </ins></h1>



The Servo connector will allow to very easily replace a faulty servo.
The second connector can be used to connect a second servo like a cutter mounted on the encoder.
The spacer will keep the drag chain in line with the chain end, and allow to secure the cables with a tie-wrap. It mounts between the drag chain and the the anchor. 

## Bom
In addition to the normal bom for those parts, you will need :
* 1 servo connectors (optionnally 2) 
  They are made for the JR/Futaba connectors found on AliExpress : https://fr.aliexpress.com/item/1005004152966553.html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
* 1 Tie-Wrap


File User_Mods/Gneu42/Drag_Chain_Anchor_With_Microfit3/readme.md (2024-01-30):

<h1 align="center"><ins>Darg chain anchor with Microfit 3 connectors </ins></h1>



This will allow to very easily remove the top part of the ERCF V2 for maintenance purpose.
It is designed to go with the Block End with bushing mods on this repo.

## Bom
In addition to the normal bom for those parts, you will need :
* 2 M3 inserts
* 2 M3x8 SHCS 
* 3 Microfit 3, 4 pins connector male
* 3 Microfit 3, 4 pins connector female  



* The connector marked "MOTOR" is used for the motor connection
* The connector marked "PWR" is used for power supply of the Binky encoder, the servo, and the status LED.
* The connector marked "Sig." is used for the signals of the Binky encoder, the servo signal, the status data signal of the status LED, and a spare pin available for what ever you need more. 

**Here is an example of the Microfit3 pinout :**



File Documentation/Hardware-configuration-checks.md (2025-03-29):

#### Page Sections:
  - [Checks You Should Have Done Already](#checks-you-should-have-done-already)
  - [Step 1. Check Endstop & Optional Sensors](#step-1-check-endstop--optional-sensors)
  - [Step 2. Check motor movement and direction](#step-2-check-motor-movement-and-direction)
  - [Step 3. Check the Encoder](#step-3-check-the-encoder)
  - [Step 4. Check other sensors (if fitted)](#step-4-check-other-sensors-if-fitted)
  - [Step 5. Check Servo](#step-5-check-servo)

*\[This guide was adapted from the [Happy Hare Wiki](https://github.com/moggieuk/Happy-Hare/wiki) for ERCF v2. Thanks Moggie!\]*

## Checks You Should Have Done Already

All of these checks and adjustments were covered in the Build Manual, and should have been done while building your ERCF.

-Filament path / BMG Gear alignment (Manual page 71)

-(if using a Geared setup) Adjustment of GT2 pulley and belt tension (Covered in the Geared Drive sub-Manual)

-Encoder path adjustment (page 114)

-Setting GT2 pulley and belt tension (page 127)

-Setting 8mm rod depth (page 136)

**If you haven't done these steps, go review the manual!**

<br>

Now that you've completed the [Happy Hare Configuration](https://github.com/Enraged-Rabbit-Community/ERCF_v2/blob/master/Documentation/Happy-Hare-Configuration.md), you should be greeted by a large warning on your console:

```yml
Prerequsite calibration steps are not complete:
Use MMU_CALIBRATE_SELECTOR to calibrate selector for gates: 0,1,2,3,4,5,6,7
Use MMU_CALIBRATE_GEAR (with gate 0 selected) to calibrate gear rotation_distance on gate: 0
Use MMU_CALIBRATE_ENCODER (with gate 0 selected)
Use MMU_CALIBRATE_GEAR (with gate selected) or MMU_CALIBRATE_GATES GATE=xx to calibrate gear rotation_distance on gates: 1,2,3,4,5,6,7
Use MMU_CALIBRATE_BOWDEN
```

That is normal, do not worry. Before we tackle that, we need to make sure all of the hardware is configured correctly!

## Step 1. Check Endstop & Optional Sensors

Verify that the Selector endstop, and any installed extruder or toolhead sensors are working. The recommended procedure is:

`MMU_MOTORS_OFF`

Now remove filament from ERCF and extruder, and move the Selector to the center of travel.

`QUERY_ENDSTOPS`

(Or use the visual query in Mainsail or Fluuid). Validate that you can see:

```yml
mmu_sel_home:open
extruder:open
toolhead:open
[...]
```

> [!NOTE]
> You will only see the sensors you have installed. You will additionally see any endstops or sensors installed on your printer.

Then manually press and hold the selector microswitch and rerun `QUERY_ENDSTOPS`.

Validate that you can see `mmu_sel_home:TRIGGERED` in the list.

If you have an extruder sensor installed, feed filament into the extruder past the switch and rerun `QUERY_ENDSTOPS`.

Validate that you can see `extruder:TRIGGERED` in the list.

If you have a toolhead sensor installed, feed filament into the toolhead past the switch and rerun `QUERY_ENDSTOPS`.

Validate that you can see `toolhead:TRIGGERED` in the list.

If any of these don't change state, then the pin assigned to the endstop is incorrect. If the state is inverted (i.e. enstop transitions to `open` when pressed) then add/remove the `!` on the respective endstop pin in `mmu_hardware.cfg`. 

Other endstops like "touch" operation and pregate sensors are advanced and are not cover by this inital setup.

## Step 2. Check motor movement and direction

Once pins are correct it is important to verify direction.  It is not possible for the installer to ensure this because it depends on the actual stepper wiring.  The recommended procedure is:

Run the command `MMU_MOTORS_OFF` Now move the Selector to the center of travel. 

Next, run the command `MMU_HOME` and verify that the Selector moves towards the endstop / home position

If the Selector doesn't move it is likley that the pin configuration for `step_pin` and/or `enable_pin` are incorrect. Open up `mmu_hardware.cfg`, and find the section `[stepper_mmu_selector]`.

Verify the pin names and prefix the pin with `!` to invert the signal. E.g.

```yml
enable_pin: !mmu:MMU_SEL_ENABLE
 (or)
enable_pin: mmu:MMU_SEL_ENABLE
```

If the selector moves the wrong way the `dir_pin` is inverted. Either add or remove the `!` prefix:

```yml
dir_pin: !mmu:MMU_SEL_DIR
 (or)
dir_pin: mmu:MMU_SEL_DIR
```

Now repeat the exercise with the gear stepper:

```yml
MMU_MOTORS_OFF
  (remove any filament from your MMU)
MMU_TEST_MOVE MOVE=100 SPEED=50
  (verify that the gear stepper would push filament towards the extruder / pull filament from the spool)
MMU_TEST_MOVE MOVE=-100 SPEED=50
  (verify that the gear stepper is pulling filament away from the extruder / pushing filament back to the spool)
```

If the gear stepper doesn't move or moves the wrong way open up `mmu_hardware.cfg`, find the section `[stepper_mmu_gear]`:<br>
If gear doesn't move it is likley that the pin configuration for `step_pin` and/or `enable_pin` are incorrect. Verify the pin names and prefix the pin with `!` to invert the signal. E.g.

```yml
enable_pin: !mmu:MMU_GEAR_ENABLE
 (or)
enable_pin: mmu:MMU_GEAR_ENABLE
```

If the gear moves the wrong way the `dir_pin` is inverted. Either add or remove the `!` prefix:

```yml
dir_pin: !mmu:MMU_GEAR_DIR
  # or
dir_pin: mmu:MMU_GEAR_DIR
```

## Step 3. Check the Encoder

We need to check that the Encoder is wired correctly. Run the command `MMU_ENCODER` and note the position displayed.

```yml
MMU_ENCODER
Encoder position: 23.4
```

Insert some filament (from either side) and pull backwards and forwards.  You should see the red LED flashing behind the enraged rabbit's eyes. Rerun `MMU_ENCODER` and validate the position displayed has increased (note that the encoder is not direction aware, so it will always increase in reading).

If the encoder postion does not change, validate the `encoder_pin` is correct. It shouldn't matter if it has a `!` (inverted) or not, but it might require a `^` (pull up resister) to function.

```yml
[mmu_encoder mmu_encoder]
encoder_pin: ^mmu:MMU_ENCODER	
```

## Step 4. Check other sensors (if fitted)

Other sensors are generally filament sensors and act on a switch. The easiest way to check these is to run something similar to the following for each sensor/switch.

```yml
QUERY_FILAMENT_SENSOR SENSOR=mmu_gate_sensor
Filament Sensor mmu_gate_sensor: filament not detected
```

Activate the sensor with a piece of filament and run again:

```yml
QUERY_FILAMENT_SENSOR SENSOR=mmu_gate_sensor
Filament Sensor mmu_gate_sensor: filament detected
```

Note that endstops / filament sensors that are wired normally open (NO) frequently require `^` (pull up resister) to correctly function.

## Step 5. Check Servo

> [!IMPORTANT] 
> The Servo Arm should *not* be installed yet for this test!

Ok, last sanity check. Check that the servo you have fitted is operational. Run this simple commmand. The servo should wiggle somewhere short of the configured 'up' and 'down' positions. Don't worry yet about calibration. That comes next.

```yml
MMU_TEST_BUZZ_MOTOR MOTOR=servo
```

You can also try:
```yml
MMU_SERVO POS=down
MMU_SERVO POS=up
```

All we are checking is that the servo is wired and operational.

> [!NOTE] 
> It is normal for the Gear motor to move back and forth slightly during a `MMU_SERVO POS=down` command. This is to ensure that the BMG gears mesh properly.

### ERCF Setup Steps:
- [Flashing Your Local MCU](https://github.com/Enraged-Rabbit-Community/ERCF_v2/blob/master/Documentation/Flashing-Local-MCU.md)
- [Installing Happy Hare](https://github.com/Enraged-Rabbit-Community/ERCF_v2/blob/master/Documentation/Installing-Happy-Hare.md)
- [Happy Hare Configuration](https://github.com/Enraged-Rabbit-Community/ERCF_v2/blob/master/Documentation/Happy-Hare-Configuration.md)
- Hardware Configuration Checks
- [Hardware Calibration](https://github.com/Enraged-Rabbit-Community/ERCF_v2/blob/master/Documentation/Hardware-Calibration.md)
- [Toolhead Distances](https://github.com/Enraged-Rabbit-Community/ERCF_v2/blob/master/Documentation/Toolhead-Distances.md)
- [Installing KlipperScreen Happy Hare](https://github.com/Enraged-Rabbit-Community/ERCF_v2/blob/master/Documentation/Installing-KlipperScreen.md)
- [Slicer Setup](https://github.com/Enraged-Rabbit-Community/ERCF_v2/blob/master/Documentation/Slicer-Setup.md)
- [Further Mods to Consider](https://github.com/Enraged-Rabbit-Community/ERCF_v2/blob/master/Documentation/Further-Mods.md)

#### Even more Happy Hare info can be found at:
- [Happy Hare Wiki](https://github.com/moggieuk/Happy-Hare/wiki)

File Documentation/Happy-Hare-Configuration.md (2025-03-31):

#### Page Sections:
-Configuration Options for ERCFv2:
  - [Necessary Updates](#---necessary-configuration-updates-for-v25)
  - [Filament Cutter Options](#---filament-cutter-options)
  - [Filament Sensor Options](#---filament-sensor-options)
  - [Pregate Sensor Options](#---pregate-sensor-options)

*\[This guide was adapted from the [Happy Hare Wiki](https://github.com/moggieuk/Happy-Hare/wiki) for ERCF v2.5. Thanks Moggie!\]*

## #f03c15 #c5f015 #1589F0 Necessary Configuration Updates for v2

1.  Open the file `config / mmu / base / mmu.cfg`. At the top of the file, beneath `\[mcu mmu\]`, add your Local MCU's CANBus UUID. If you are using USB to connect, Happy Hare should have detected and filled your serial number in for you. If not, you must add it in at this point. Save and close the file.

2. Open the file `config / mmu / base / mmu_hardware.cfg`. If you are using a beefy NEMA17 motor for Direct Drive, you need to increase your motor currents starting on *line 128*.

The Gear Motor `run_current` should be set to *either* 70% of the motor's peak current rating, *or* the stepper driver's maximum rated current, *whichever is less.* The max for for 2209 EZ Drivers is 1.3 amps without cooling and 1.6 amps with cooling. 

For the BOM 1.0 amp motor, this is 0.7 amps.

3. Still in the file `config / mmu / base / mmu_hardware.cfg`. If you are using Direct Drive, comment out the Gear Ratio on line 143 by adding a hash, like this:

`#gear_ratio: 80:20			# E.g. ERCF 80:20, Tradrack 50:17`

If you are using legacy Geared Drive, you instead need the Gear Ratio to be set to match your physical gear ratio, usually 80:20 or 60:20. These numbers represent the number of teeth on the 80- or 60-tooth gears, and the 20-tooth pulley.

4. Still in the file `config / mmu / base / mmu_hardware.cfg`, on *lines 164-165*:

You want the Selector Motor `run_current` to be set to 70% of the motor's peak current rating, and the `hold_current` should be about 40% of the peak current rating.

For the BOM 1.0 amp motor, this is 0.7 amps and 0.4 amps.

Save and close the file.

## #f03c15 #c5f015 #1589F0 Filament Cutter Options

If you are using a Filament Cutter, you must update `config / mmu / base / mmu_parameters.cfg` line 334. Change the `form_tip_macro` value to `_MMU_CUT_TIP`.

> [IMPORTANT]
> If you are using a fixed cutter depressor on a gantry printer (eg Voron v2.4), there is a chance that your drag chain can catch on the depressor! You will need to create a custom Macro to wrap `_MMU_CUT_TIP` into that safely moves the toolhead into position with the depressor, like so:

```yml
[gcode_macro _MMU_SAFE_CUT_TIP]
gcode:
  G0 X50 F12000
  G0 Y305
  _MMU_CUT_TIP
  G0 X50
  G0 Y250
```

**(Do not use this without changing it! Your movement values are guaranteed to differ!)**

Instead of setting the `form_tip_macro` to `_MMU_CUT_TIP` as above, put your "safe" cutting macro with the rest of your non-MMU macros (eg. in `printer.cfg`), then set `form_tip_macro` to the name of your safe cutting macro, in this example, `_MMU_SAFE_CUT_TIP`.

Next, you will need to go through the entire file `config / mmu / base / mmu_macro_vars.cfg`. Read it, understand it, and change all of the options to suit your unique build and needs. The values you use depend on which extruder / toolhead you are using. See [Toolhead Distances](https://github.com/Enraged-Rabbit-Community/ERCF_v2/blob/master/Documentation/Toolhead-Distances.md) for more details, but don't forget to do the hardware configuration and calibration steps first!

Critical variables to change include setting `variable_simple_tip_forming` to `False` and setting the `variable_pin_loc_xy`, but you should really *at least* review the **Movement** and **Cut Tip** sections. These control parking and tip cutting settings and variables.

## #f03c15 #c5f015 #1589F0 Filament Sensor Options

If you are using a toolhead with either an extruder sensor (before the extruder gears), a Toolhead sensor (after the Extruder gears), or both, you need to set those up.

1. Open the file `config / mmu / base / mmu_hardware.cfg`. Add the pin number(s) that your sensor(s) are connected to on lines 278-279. Save and close the file.

2. If you are using an extruder sensor specifically: Open the file `config / mmu / base / mmu_parameters.cfg`. Update the `extruder_homing_endstop` to use the value`extruder`. Save and close the file.

<!--> [!NOTE]
> If you are using a toolhead board like Nitehawk SB or the HartK ERCF toolhead board, all of the config for the toolhead board must be included *before* the MMU config, so that the MMU config can reference the pins needed!--> 

3. If you are using **both** an extruder **and** a toolhead sensor: reopen the file `config / mmu / base / mmu_parameters.cfg`. Update the `extruder_force_homing` to use the value`1`. This will ensure that during loading, the filament slows down before hitting the extruder gears, instead of crashing through them to the toolhead sensor. Save and close the file.

There are instructions for nearly-automatic calibration for almost all of the cutter and toolhead length values in the Happy Hare Wiki's [Blobbing and Stringing page](https://github.com/moggieuk/Happy-Hare/wiki/Blobbing-and-Stringing). Automatic calibration will make your life easier, you should do it.

## #f03c15 #c5f015 #1589F0 Pregate Sensor Options

Coming soon! I don't use these yet, so I need help writing this section!

### ERCF Setup Steps:
- [Flashing Your Local MCU](https://github.com/Enraged-Rabbit-Community/ERCF_v2/blob/master/Documentation/Flashing-Local-MCU.md)
- [Installing Happy Hare](https://github.com/Enraged-Rabbit-Community/ERCF_v2/blob/master/Documentation/Installing-Happy-Hare.md)
- Happy Hare Configuration
- [Hardware Configuration Checks](https://github.com/Enraged-Rabbit-Community/ERCF_v2/blob/master/Documentation/Hardware-configuration-checks.md)
- [Hardware Calibration](https://github.com/Enraged-Rabbit-Community/ERCF_v2/blob/master/Documentation/Hardware-Calibration.md)
- [Toolhead Distances](https://github.com/Enraged-Rabbit-Community/ERCF_v2/blob/master/Documentation/Toolhead-Distances.md)
- [Installing KlipperScreen Happy Hare](https://github.com/Enraged-Rabbit-Community/ERCF_v2/blob/master/Documentation/Installing-KlipperScreen.md)
- [Slicer Setup](https://github.com/Enraged-Rabbit-Community/ERCF_v2/blob/master/Documentation/Slicer-Setup.md)
- [Further Mods to Consider](https://github.com/Enraged-Rabbit-Community/ERCF_v2/blob/master/Documentation/Further-Mods.md)

#### Even more Happy Hare info can be found at:
- [Happy Hare Wiki](https://github.com/moggieuk/Happy-Hare/wiki)

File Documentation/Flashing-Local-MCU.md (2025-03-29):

*These instructions were copied from the manuals provided by BTT, FysEtc, and Tircown and updated for ERCF v2.*

> [!IMPORTANT] 
> These instructions assume you already have CAN communication working on your printer (unless you're using a USB connection). If you don't, check out [Esoterical's CANBus Guide](https://canbus.esoterical.online/).

**Click on the relevant headings for your mainboard:**

<details>
<summary>Flashing Katapult onto MMBv1.1</summary>

> **NOTE**
> Katapult (formerly CanBoot) is for updating MCU firmware directly via CAN Bus. If you prefer to update your firmware via USB (DFU Mode), skip this entire section.

To flash Katapult onto Raspberry Pi or CB1, refer to the following instructions to download the Katapult project: https://github.com/Arksine/katapult

1. Connect to CB1/Raspberry Pi via SSH and enter the command `cd ~` to go to the home directory.
Use the command `git clone https://github.com/Arksine/katapult` to download the Katapult project. Then enter `cd katapult` to navigate to the Katapult directory.

2. Enter `make menuconfig` and configure as shown in the provided image:

Katapult Firmware Options

3. Use the command `make` to compile the firmware. The resulting katapult.bin file will be in the home/username/katapult/out folder. This can be directly downloaded to your computer from the SSH software's left panel.

Katapult binary download

4. Hold the Boot button and connect the board to Raspberry Pi/CB1 via Type-C cable to enter DFU mode.

5. Enter `lsusb` in the SSH terminal to query the DFU device ID.

Querying DFU devide ID

6. Enter the following command to flash Katapult: `make flash FLASH_DEVICE=0483:df11`

> **NOTE**
> Replace `0483:df11` with the actual device ID found in the previous step.

7. After flashing, disconnect the Type-C cable.
</details>

---

<details>
<summary>Compiling Klipper Firmware for MMBv1.1</summary>

1. Connect to CB1/Raspberry Pi via SSH and enter the following commands:
`cd ~/klipper/`
`make menuconfig`

Configure the firmware as shown in the provided image (update Klipper firmware to the latest version if options are not available).

Querying DFU devide ID

`[*] Enable extra low-level configuration optionsMicro-controller`

`Micro-controller Architecture (STMicroelectronics STM32) --->`

`Processor model (STM32G0B1) --->`

If not using Katapult:

`Bootloader offset (No bootloader) --->`

If using Katapult:

`Bootloader offset (8KiB bootloader) --->`

If USB communication on Type-C is used:

`Communication interface (USB (on PA11/PA12)) --->`

If CAN-Bus communication is used:

`Communication interface (CAN bus (on PB0/PB1)) --->`
`(1000000) CAN bus speed`

2. After configuration, press `q` to exit, and select `Yes` when prompted to save.

3. Enter `make` to compile the firmware. The resulting `klipper.bin` file will be in the `home/username/klipper/out` folder. This can be directly downloaded to your computer from the SSH software's left panel.

Klipper binary download

</details>

---

<details>
<summary>Flashing Katapult onto MMBv2.0</summary>

> **NOTE** 
> Katapult (formerly CanBoot) is for updating MCU firmware directly via CAN bus. If you prefer to update via USB (DFU Mode), skip this entire section.

To flash Katapult onto Raspberry Pi or CB1, refer to the following instructions to download the Katapult project: https://github.com/Arksine/katapult

1. Connect to CB1/Raspberry Pi via SSH and enter the command `cd ~` to go to the home directory.
Use the command `git clone https://github.com/Arksine/katapult` to download the Katapult project. Then enter `cd katapult` to navigate to the Katapult directory.

2. Enter `make menuconfig` and configure as shown in the provided image:

Katapult Firmware Options

3. Use the command `make` to compile the firmware. The resulting katapult.bin file will be in the home/username/katapult/out folder. This can be directly downloaded to your computer from the SSH software's left panel.

Katapult binary download

4. Hold the Boot button and connect the board to Raspberry Pi/CB1 via Type-C cable to enter DFU mode.

5. Enter `lsusb` in the SSH terminal to query the DFU device ID.

Querying DFU devide ID

6. Enter the following command to flash Katapult: `make flash FLASH_DEVICE=0483:df11`

> **NOTE**
> Replace `0483:df11` with the actual device ID found in the previous step.

7. After flashing, disconnect the Type-C cable.

</details>

---

<details>
<summary>Compiling Klipper Firmware for MMBv2.0</summary>

1. Connect to CB1/Raspberry Pi via SSH and enter the following commands:
`cd ~/klipper/`
`make menuconfig`

Configure the firmware as shown in the provided image (update Klipper firmware to the latest version if options are not available).

Querying DFU devide ID

`[*] Enable extra low-level configuration optionsMicro-controller`

`Micro-controller Architecture (STMicroelectronics STM32) --->`

`Processor model (STM32G0B1) --->`

If not using Katapult:

`Bootloader offset (No bootloader) --->`

If using Katapult:

`Bootloader offset (8KiB bootloader) --->`

If USB communication on Type-C is used:

`Communication interface (USB (on PA11/PA12)) --->`

If CAN-Bus communication is used:

`Communication interface (CAN bus (on PD0/PD1)) --->`
`(1000000) CAN bus speed`

2. After configuration, press `q` to exit, and select `Yes` when prompted to save.

3. Enter `make` to compile the firmware. The resulting `klipper.bin` file will be in the `home/username/klipper/out` folder. This can be directly downloaded to your computer from the SSH software's left panel.

Klipper binary download

</details>

---

<details>
<summary>Firmware Update via Katapult for MMB (CANBus only)</summary>

Guide to update Raspberry Pi / CB1 / primary MCU via CANBus using Katapult. These steps are identical for MMBv1.1 and MMBv2.0.

1. Connect the CAN bus cable and plug a jumper at the 120R terminal resistor.

2. Enter the command `cd ~/katapult/scripts` then enter `python3 flash_can.py -i can0 -q`
This will query the canbus ID (make sure the CAN cable is connected and powered on) as shown in the figure below, the UUID of the device has been found:

Querying CANBus UUID

3. Enter `python3 flash_can.py -i can0 -f ~/klipper/out/klipper.bin -u be69315a613c`

> **NOTE** 
> Replace `be69315a613c` with the actual device UUID found in the previous step.

klipper.bin needs to be generated in advance using the `make` command, and the application start offset of Katapult is 8KiB offset, so Klipper's menuconfig Bootloader offset should also be 8KiB bootloader as shown in the following figure.

CANBus Flashing Success

4. Query again with `python3 flash_can.py -i can0 -q`
The Application should now show Klipper, indicating it is running correctly.

Klipper flashing success
</details>

---

<details>
<summary>Firmware Update for MMB using USB (DFU Mode)</summary>

Guide to update Raspberry Pi / CB1 / primary MCU via USB (DFU Mode). These steps are identical for MMBv1.1 and MMBv2.0.

1. Hold the Boot button and connect the MMB to Raspberry Pi/CB1 via Type-C cable to enter DFU mode.

2. Enter `lsusb` in the SSH terminal to query the DFU device ID.

Querying DFU Mode Device ID

3. Enter `cd klipper` to navigate to the Klipper directory, and enter:

`make flash FLASH_DEVICE=0483:df11`

> **NOTE **
> Replace `0483:df11` with the actual device ID found in the previous step.

This will start flashing the firmware.

4. After flashing, enter `ls /dev/serial/by-id/` to query the device's Serial ID (only applicable for USB communication, not for CANBus).

5. If you are using USB communication, you don't need to press the Boot button for subsequent updates. You can enter the following command to flash the firmware:

`make flash FLASH_DEVICE=/dev/serial/by-id/usb-Klipper_stm32g0b1xx_4550357128922FC8-if00`

> **NOTE**
>  Replace `/dev/serial/by-id/xxx` with the actual ID found in the previous step.

6. If you are using CAN bus for communication, disconnect the Type-C cable after flashing.

</details>

---

<details>
<summary>Compiling and flashing Klipper onto EASY-BRD</summary>

This guide assumes you are using the version with Seeeduino XIAO.
Other microcontrollers configurations are available in [config](https://github.com/Tircown/ERCF-easy-brd/blob/master/config/Seeeduino%20XIAO%20-%20SAMD21G18/ercf_hardware.cfg).

* Install bossac (version ≥1.8)
```
sudo apt install libreadline-dev libwxgtk3.0-*
git clone https://github.com/shumatech/BOSSA.git
cd BOSSA
make
sudo cp bin/bossac /usr/local/bin
```
* Prepare the firmware
```
cd ~/klipper
make menuconfig
```
Menuconfig instructions
```
make clean
make
```
* Flashing the Seeeduino XIAO
Connect the Seeeduino XIAO to your raspberry if it's not already done.
Get the port of the XIAO, i.e. `ls /dev/tty*`, and modify the default `/dev/ttyACM1` in the command line bellow.
Use tweezers or short lines to short the RST pins in the diagram twice. The orange LED lights flicker on and light up. Then send in the next few seconds this command line matching your port.
```
sudo /usr/local/bin/bossac -i -d -p /dev/ttyACM1 -e -w -v -R --offset=0x2000 out/klipper.bin
```

More informations on how to reset for flashing:
https://wiki.seeedstudio.com/Seeeduino-XIAO/#enter-bootloader-mode
</details>

---

<details>
<summary>Other EASY-BRD MCU configurations</summary>

See [ercf_hardware.cfg](https://github.com/Tircown/ERCF-easy-brd/blob/master/config/Seeeduino%20XIAO%20-%20SAMD21G18/ercf_hardware.cfg) for the Seeeduino XIAO (most common solution)
Other microcontrollers configurations are available in config.
</details>

---

<details>
<summary>Compiling Klipper for ERBv1.0</summary>

### Compile options
On your klipper device (usually Raspberry Pi) run the following to create your make configuration:

```shell
cd  ~/klipper
make clean
make menuconfig
```

Select the following menuconfig settings

makemenuconfig

And create the firmware files by running the following:

```shell
make
```

</details>

---

<details>
<summary>Flashing Firmware onto ERBv1.0</summary>

#### 1.With your windows PC

Step 1: Connect 24V (Power on the board)

Step 2: Connect USB-C cable to your Klipper device (usually Raspberry Pi)

Step 3: Push and hold the BOOTSEL button

Step 4: Push the RST button and hold 0.5 seconds

Step 5: Release the RST button, after 3 seconds, Release the bootsel button

Step 6: `RPI-RP2` folder will show up on your computer, copy your built firmware `klipper.uf2` to the folder.





#### 2. With your Pi 

Thanks for mk-maddin's work:
https://github.com/FYSETC/FYSETC-ERB/issues/2#issuecomment-1618902635

##### Connecting the board and bring it into flash mode

Step 1: Connect 24V (Power on the board)

Step 2: Connect USB-C cable to your Klipper device (usually Raspberry Pi)

Step 3: Push and hold the BOOTSEL button

Step 4: Push the RST button and hold 0.5 seconds

Step 5: Release the RST button, after 3 seconds, Release the bootsel button

Verify your device is in boot mode connected by running the following command:

```shell
lsusb
```

The output should contain an entry looking like 2e8a:0003 Raspberry Pi RP2 Boot


##### Flashing the firmware
Now we do not flash the fimware by directly copying it to the storage, but we flash it using the following command:

```shell
make flash FLASH_DEVICE=2e8a:0003
```

The output looks like the following - IF you are prompted (you might or might not) for a password, enter the password of your current user account.


Now restart your fystec-erb by disconnecting 24V - waiting some seconds and reconnecting 24V again.
You should be able to see it as usual klipper device within 
```shell
ls /dev/serial/by-id
```

### Configuration

See `ercf_hardware.cfg` in the ERBv1.0 repository [config](https://github.com/FYSETC/FYSETC-ERB/tree/main/V1.0/config) folder.

### Known issues

The mark of GPIO24 and GPIO25 is swapped, check the silk file [here](https://github.com/FYSETC/FYSETC-ERB/blob/master/hardware/Silk%20Fixed.pdf).
</details>

---

<details>
<summary>Compiling and Flashing Klipper onto ERBv2.0</summary>

### Compile and upload
In order to compile and upload at one time, you need to follow the steps below to put RP2040 into dfu mode.

1. Step 1: Connect 24V (Power on the board)
2. Step 2: Connect USB-C cable to your Klipper device (usually Raspberry Pi)
3. Step 3: Push and hold the BOOTSEL button
4. Step 4: Push the RST button and hold 0.5 seconds
5. Step 5: Release the RST button, after 3 seconds, Release the bootsel button
6. Verify your device is in boot mode connected by running the following command:

```shell
lsusb
```

The output should contain an entry looking like 2e8a:0003 Raspberry Pi RP2 Boot


On your klipper device (usually Raspberry Pi) run the following to create your make configuration:

```shell
cd  ~/klipper
make clean
make menuconfig
```

Select the following menuconfig settings

Use USB communication



Use CANBUS communication



And create and upload the firmware files by running the following:

```shell
make flash FLASH_DEVICE=2e8a:0003
```
The output looks like the following - IF you are prompted (you might or might not) for a password, enter the password of your current user account.


Now restart your fystec-erb by disconnecting 24V - waiting some seconds and reconnecting 24V again.
Or press the reset button for one second and then release it.
You should be able to see it as usual klipper device within 
```shell
ls /dev/serial/by-id
```
### Configuration

See `ercf_hardware.cfg` in the ERBv2.0 repository [config](https://github.com/FYSETC/FYSETC-ERB/tree/main/V2.0/config) folder.

---------------------------------------------------

> **TIP**
> We recommend using the Katapult bootloader, whether you use USB or CANBUS communication. This can avoid many strange problems.
> 
> Configuration of the Katapult bootloader:
> 
> ERBv2_katakulpt_menuconfig_USB
> ERBv2_katakulpt_menuconfig_CAN
> 
> Configuration of klipper using Katapult:
> 
> ERBv2_menuconfig_16kb_USB
> ERBv2_menuconfig_16kb_CAN

</details>

---

### ERCF Setup Steps:
- Flashing Your Local MCU
- [Installing Happy Hare](https://github.com/Enraged-Rabbit-Community/ERCF_v2/blob/master/Documentation/Installing-Happy-Hare.md)
- [Happy Hare Configuration](https://github.com/Enraged-Rabbit-Community/ERCF_v2/blob/master/Documentation/Happy-Hare-Configuration.md)
- [Hardware Configuration Checks](https://github.com/Enraged-Rabbit-Community/ERCF_v2/blob/master/Documentation/Hardware-configuration-checks.md)
- [Hardware Calibration](https://github.com/Enraged-Rabbit-Community/ERCF_v2/blob/master/Documentation/Hardware-Calibration.md)
- [Toolhead Distances](https://github.com/Enraged-Rabbit-Community/ERCF_v2/blob/master/Documentation/Toolhead-Distances.md)
- [Installing KlipperScreen Happy Hare](https://github.com/Enraged-Rabbit-Community/ERCF_v2/blob/master/Documentation/Installing-KlipperScreen.md)
- [Slicer Setup](https://github.com/Enraged-Rabbit-Community/ERCF_v2/blob/master/Documentation/Slicer-Setup.md)
- [Further Mods to Consider](https://github.com/Enraged-Rabbit-Community/ERCF_v2/blob/master/Documentation/Further-Mods.md)

#### Even more Happy Hare info can be found at:
- [Happy Hare Wiki](https://github.com/moggieuk/Happy-Hare/wiki)

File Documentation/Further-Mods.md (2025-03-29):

## #f03c15 #c5f015 #1589F0 Further Mods to Consider

A toolhead filament cutter (eg Filametrix) or Selector filament cutter (eg EREC) will remove the need to tune your filament tips. It is widely considered to be a very worthwhile modification, because [tip tuning](https://github.com/moggieuk/Happy-Hare/wiki/Tip-Forming-and-Purging) is a lengthy manual process that must be done for each new filament type and brand, and potentially even for each color or batch of filament. Toolhead cutters are recommended over Selector filament cutters because of the chance for strings of filament to be left in the Bowden tube.

Extruder and/or toolhead filament sensors are also recommended options because they add more automation to Happy Hare's functionality. All toolhead distances can be automatically derived when using both sensors - without them, some amount of trial and error is needed to adjust the toolhead distances. This is important for both loading, unloading, and ooze prevention.

Because there are a multitude of different extruders and toolheads, there is no single cut-and-dry solution for toolhead filament cutters or sensors. The ERCF team is working on developing suitable first-part extruder and toolhead options. One of the first to be released after ERCF v2.5 is out of beta will be a modified Clockwork2 extruder with dual sensor options, a toolhead cutter, and other quality-of-life improvements. Stay tuned!

[Blobifier](https://github.com/Dendrowen/Blobifier) is a modification that allows for purging filament to pellets, instead of using a Wipe Tower. Happy Hare includes optional support for Blobifier that can be enabled either during initial setup.

### ERCF Setup Steps:
- [Flashing Your Local MCU](https://github.com/Enraged-Rabbit-Community/ERCF_v2/blob/master/Documentation/Flashing-Local-MCU.md)
- [Installing Happy Hare](https://github.com/Enraged-Rabbit-Community/ERCF_v2/blob/master/Documentation/Installing-Happy-Hare.md)
- [Happy Hare Configuration](https://github.com/Enraged-Rabbit-Community/ERCF_v2/blob/master/Documentation/Happy-Hare-Configuration.md)
- [Hardware Configuration Checks](https://github.com/Enraged-Rabbit-Community/ERCF_v2/blob/master/Documentation/Hardware-configuration-checks.md)
- [Hardware Calibration](https://github.com/Enraged-Rabbit-Community/ERCF_v2/blob/master/Documentation/Hardware-Calibration.md)
- [Toolhead Distances](https://github.com/Enraged-Rabbit-Community/ERCF_v2/blob/master/Documentation/Toolhead-Distances.md)
- [Installing KlipperScreen Happy Hare](https://github.com/Enraged-Rabbit-Community/ERCF_v2/blob/master/Documentation/Installing-KlipperScreen.md)
- [Slicer Setup](https://github.com/Enraged-Rabbit-Community/ERCF_v2/blob/master/Documentation/Slicer-Setup.md)
- Further Mods to Consider

#### Even more Happy Hare info can be found at:
- [Happy Hare Wiki](https://github.com/moggieuk/Happy-Hare/wiki)

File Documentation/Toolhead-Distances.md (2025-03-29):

#### Page Sections:
- [Correct Meaning of Key Dimensions](#---correct-meaning-of-key-dimensions)
- [Calibrating Toolhead](#---calibrating-toolhead)
  - [Final Blob Tuning](#---final-blob-tuning---toolhead_ooze_reduction)
  - [Toolchange Retraction](#---tool-change-retraction)
  - [Z-Hop and Ramping](#---z-hop-and-ramping)
- [Summary of Tuning Steps](#---summary-of-tuning-steps)
- [Cleaning Extruder with Cold Pull](#---cleaning-extruder-with-a-cold-pull)

<br>

This discussion assumes that you have initial setup complete and are now ready to tune the quality of your prints. Although some of the information contained here is useful early in your journey it will make a lot more sense once you have some experience with default or "borrowed" toolhead parameters. You *must* configure and calibrate your hardware before doing this step.

This guide will then guide you to optimize a few critical parameters for print quality that avoids blobbing on your wipetower or print and stringing when moving to change tool.

Specifically in this guide you will learn how to correctly set the following parameters (`mmu/base/mmu_parameters.cfg`):
- `toolhead_extruder_to_nozzle`
- `toolhead_sensor_to_nozzle`
- `toolhead_entry_to_extruder`
- `toolhead_residual_filament`
- `toolhead_ooze_reduction`

It will also illustrate how to use z-hop movement/ramping and retraction settings to eliminate blobs and stringing during color changes or EndlessSpool operations in your prints (`mmu/base/mmu_macro_vars.cfg`):
- `variable_park_toolchange`, `variable_park_mmu_error`, `variable_park_pause`, `variable_park_cancel`, `variable_park_complete`
- `variable_restore_xy_pos`
- `variable_park_travel_speed`, `variable_park_lift_speed`
- `variable_retract`, `variable_retract_speed`, `variable_unretract_speed`

And finally, set key tip cutting macro variables (`mmu/base/mmu_macros_vars.cfg`):
- `variable_blade_pos`
- `variable_retract_length`

<br>

## #f03c15 #c5f015 #1589F0 Correct Meaning of Key Dimensions

Firstly it is important to understand that while sensors like a toolhead sensor can help with extruder loading and unloading, the process relies on precise movement distances. These "dimensions" often interact with each other so it is also important that they are set correctly and match the meaning Happy Hare is expecting. Doing so will give deterministic toolchanges rather than a "these settings seem to work" scenario.
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

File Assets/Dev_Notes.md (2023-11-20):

## CAD Design Guidelines (in case you were interested)
* No overhangs over 45 degrees
* No supports (unless they are absolutely needed, and if that's the case they must be built in to the part)
* 0.4mm chamfer on surfaces that touch the print bed (and no fillets on the build surface--breaks the 45 degree overhang rule)
* General "nice" aesthetic
* Take note of part orientation to make sure the part is strong in the directions it needs to be.
* Countersunk holes "overhanging" the print surface should have a chamfer on them or other method like that to prevent issues
* Think about minimum perimeters/shells--try to avoid really thin features
* Design with common screws/hardware in mind. Ie, stick with M3x6,8,12,16,20,25,30,35,40, M5x10,16,30,40 when possible (for V1/V2)
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

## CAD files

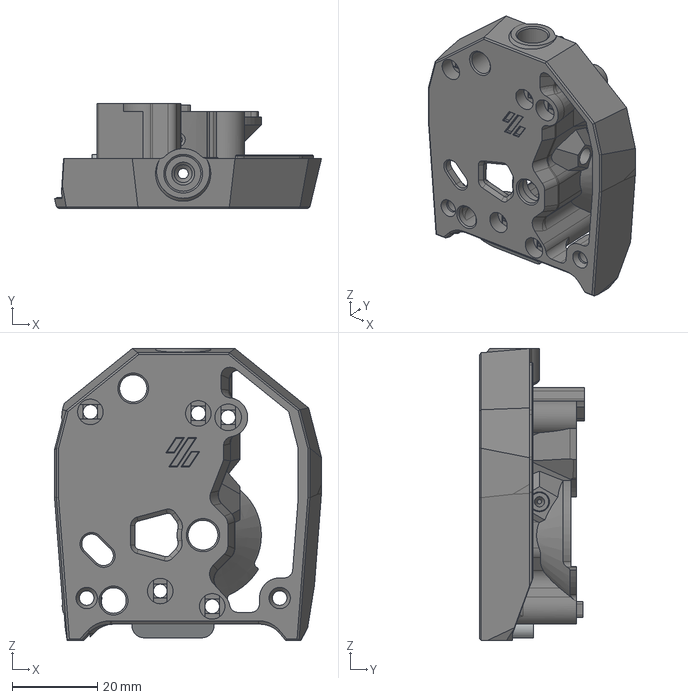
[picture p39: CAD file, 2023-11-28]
Recommended_Options/ERF_Filament_Cutter/CAD/SB_CW2_Main_Body_Cutting_With_ECAS.step
62.8 x 24.7 x 68.7 mm

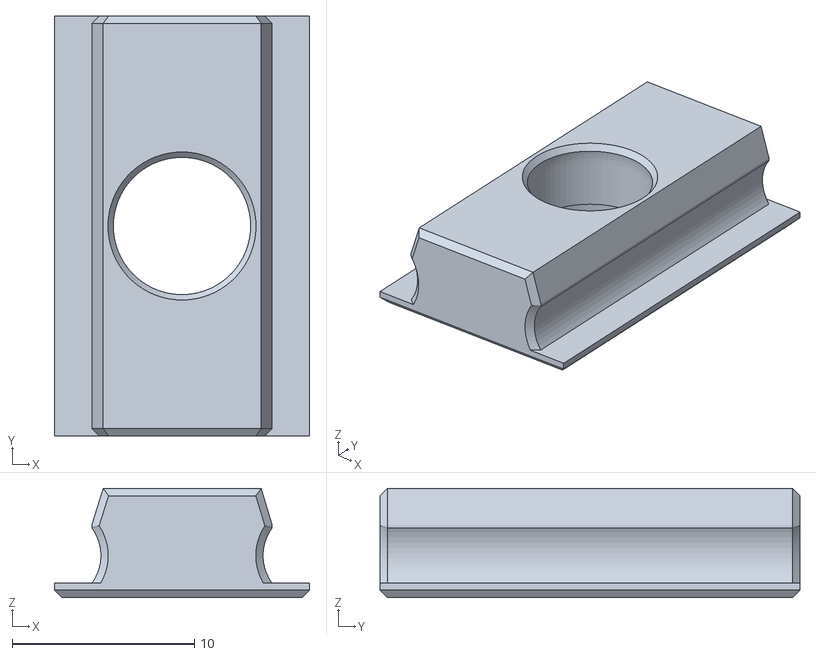
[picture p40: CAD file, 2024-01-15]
_Errata/Apron_LED_no_multi-color/Cover_Body_xN.stl
14.0 x 23.0 x 5.98

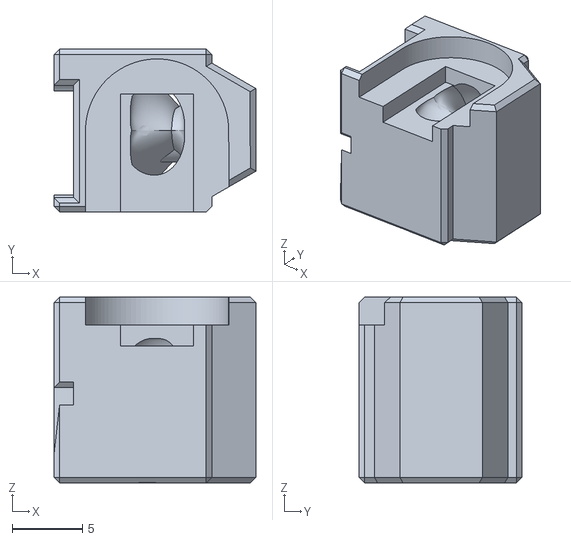
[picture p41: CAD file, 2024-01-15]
_Errata/Encoder_with_Status_LED/623ZZ_Bearing/Encoder_for_623ZZ_bearing_Exit_LED_Insert.stl
14.4 x 11.6 x 13.2

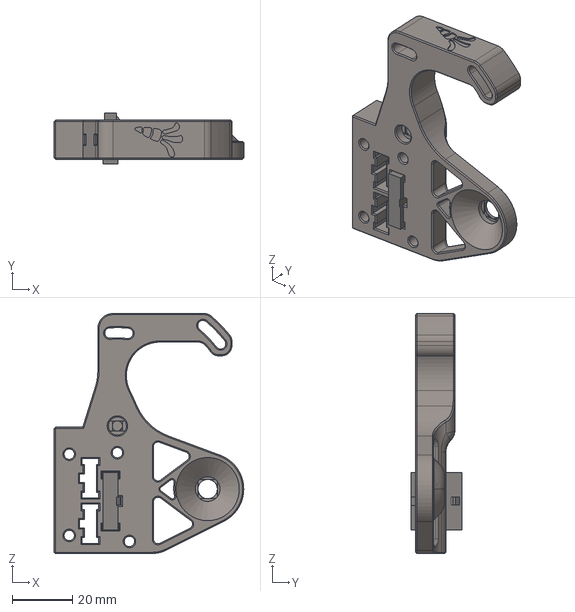
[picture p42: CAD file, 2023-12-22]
_Errata/Motor_Arm_NEMA17_GS-6pins.step
63.0 x 16.9 x 79.7 mm

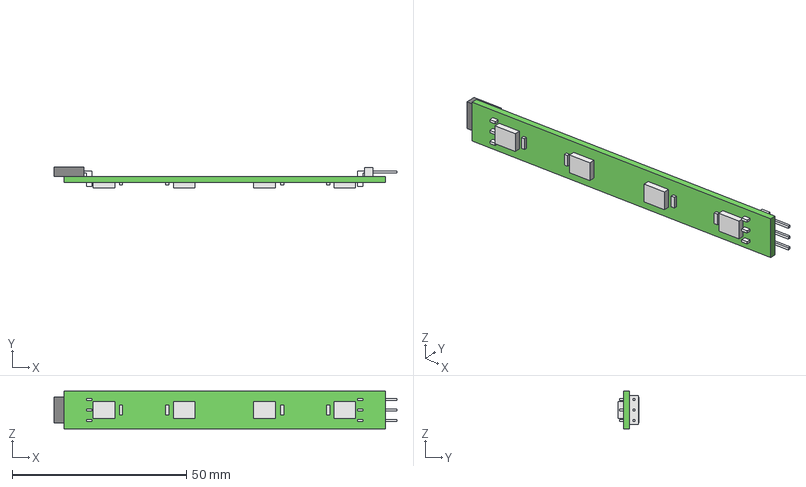
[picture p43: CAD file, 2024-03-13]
CAD/Misc/Apron_Neopixels/ERCF Carrot on a Stick v2.step
98.6 x 6.05 x 10.9 mm
LEDs
Capacitors
PCB
Connector
Header Comb
Header 1
Header 2

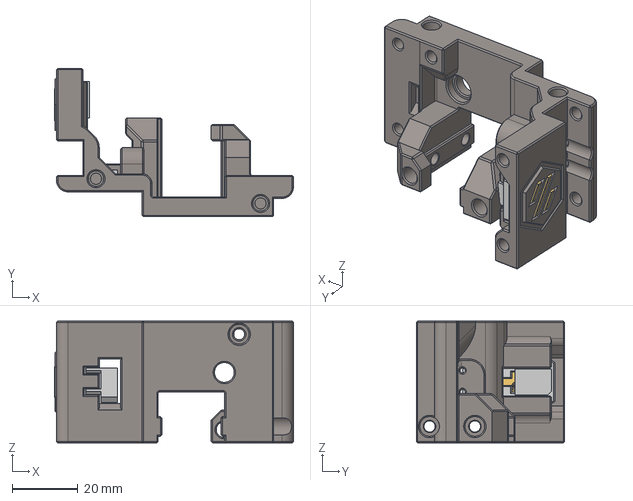
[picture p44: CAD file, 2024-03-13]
CAD/Misc/Gear_Box_Front_With_LED.step
72.6 x 45.0 x 37.0 mm
Diffuser
Barf holder

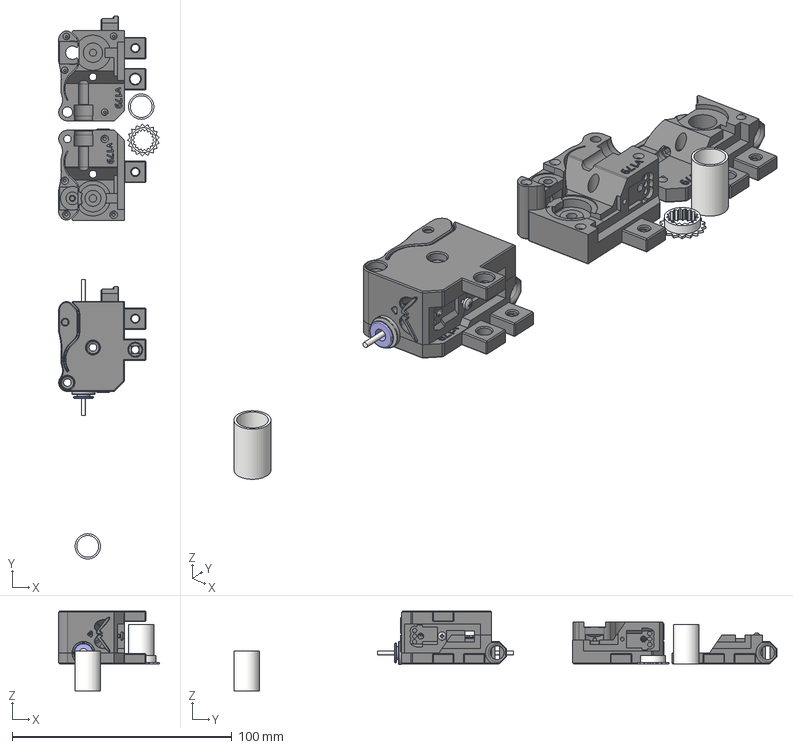
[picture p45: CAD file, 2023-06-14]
CAD/work_in_progress/EncoderCart - Binky.step
45.8 x 246.9 x 36.2 mm
Magnet6x3 v1 (3)
Magnet6x3 v1 (1) (1)
M3x8SHCS v1 (1)
M3x16 SHCS (2)^Fan Assembly (1)_X Carriage (2) (1) x 3
M3 Threaded Insert (1)^VORON Clockwork_X Carriage x 3
Main body (1)
Release clip (1)
Seal (1)
ECAS - Clearance
stift 3 x 20 (1)^Direct_Drivegear_without_setscrew (1)_Guidler_VORON Clockwork_X Carriage (1)
K3x5x7 Needlebearing (1)^Direct_Drivegear_without_setscrew (1)_Guidle r_VORON Clockwork_X Carriage (1) x 2
Direct_Drivegear_without_setscrew (1)-39^Direct_Drivegear_without_set screw (1)_Guidler_VORON Clockwork_X Carriage (1)
Encoder_Cart_SlottedWheel
Screw - 2x10mm - Philips Button Head
Filament
Encoder_SlottedWheel_PushTool x 2
Encoder_Cart_SlottedWheel_1
Encoder_Right x 2
Encoder_Left x 2

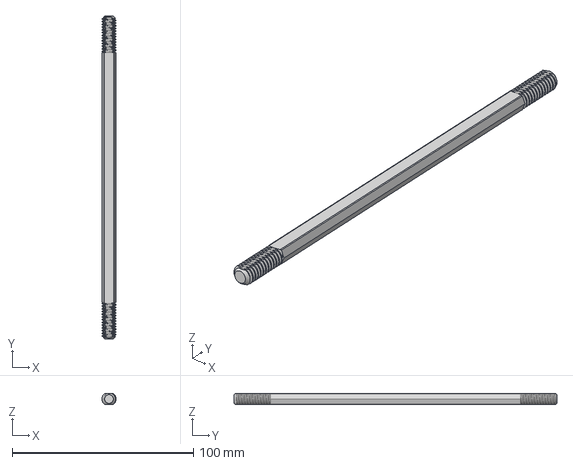
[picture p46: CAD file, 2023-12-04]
Recommended_Options/ERCT_Buffer/CAD/STEP/Axle/Axle_6_Double_Thread.step
7.90 x 178.0 x 5.94 mm

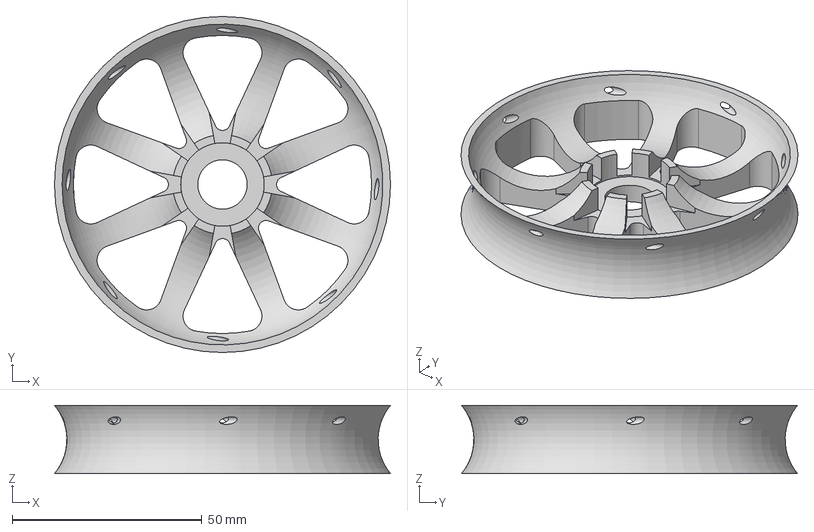
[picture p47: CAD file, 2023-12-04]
Recommended_Options/ERCT_Buffer/CAD/STEP/Buffer_Wheel/Buffer_Wheel_xN.step
88.5 x 88.5 x 17.9 mm

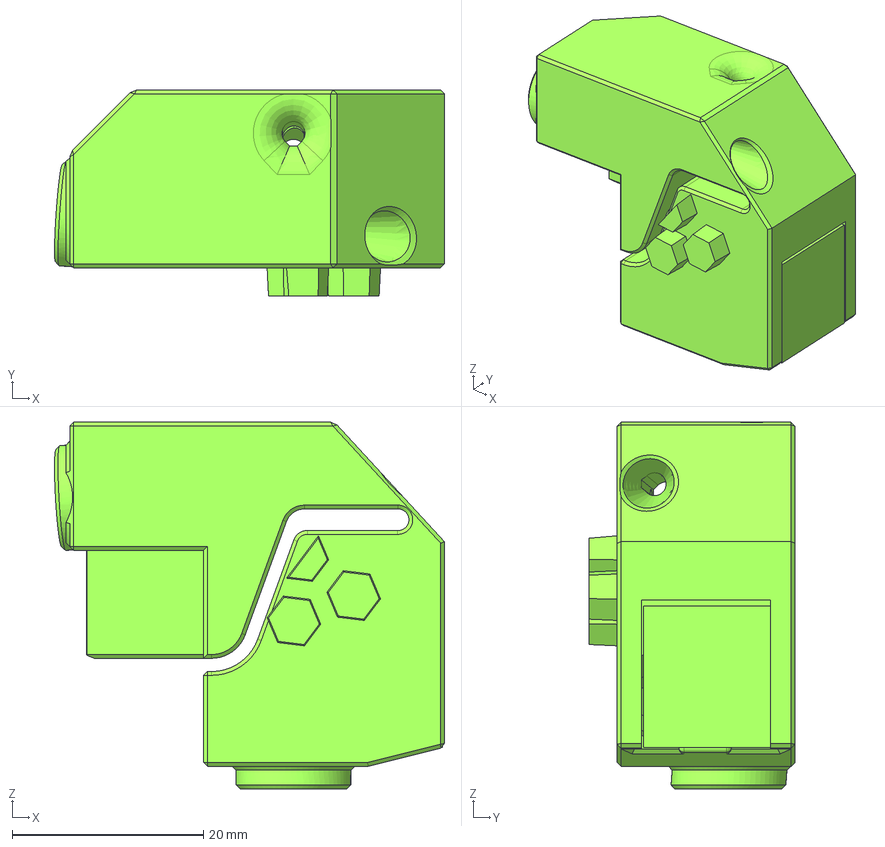
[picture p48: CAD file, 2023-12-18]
Recommended_Options/ERCT_Buffer/CAD/STEP/Coupler_Block/Coupler_Block_MMB_v3_Microswitch.step
40.8 x 21.6 x 38.3 mm

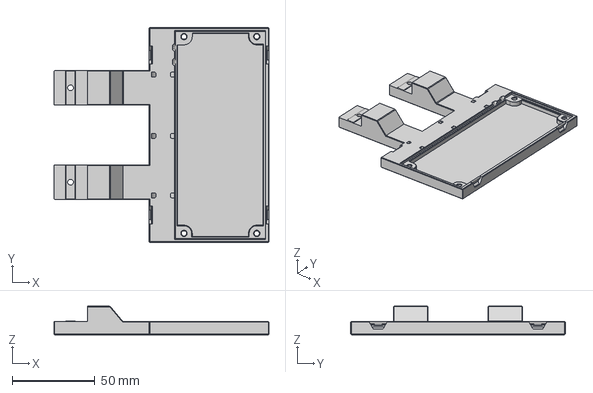
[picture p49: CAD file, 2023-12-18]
Recommended_Options/ERCT_Buffer/CAD/STEP/MMB_Rear_Mount/[a]BTT_MMB_rear_mount.step
130.0 x 129.8 x 17.2 mm

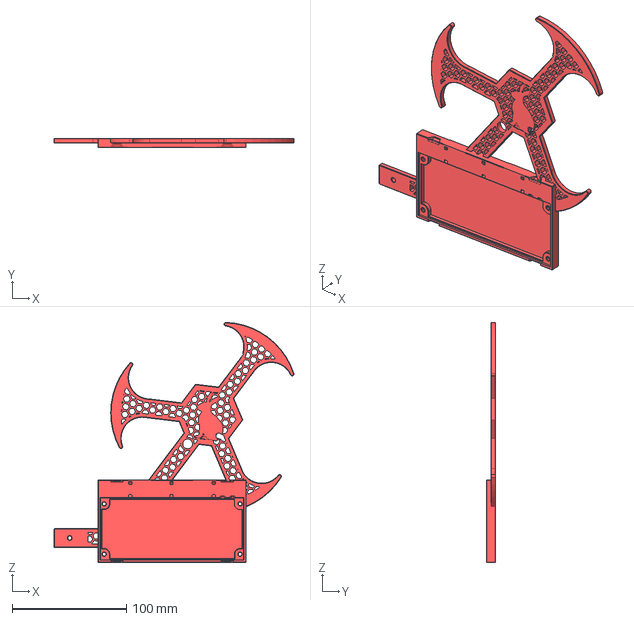
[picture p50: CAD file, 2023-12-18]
Recommended_Options/ERCT_Buffer/CAD/STEP/Support_Arms/[a]_Support_Arm_Endcap_With_MMB.step
210.1 x 8.05 x 210.4 mm

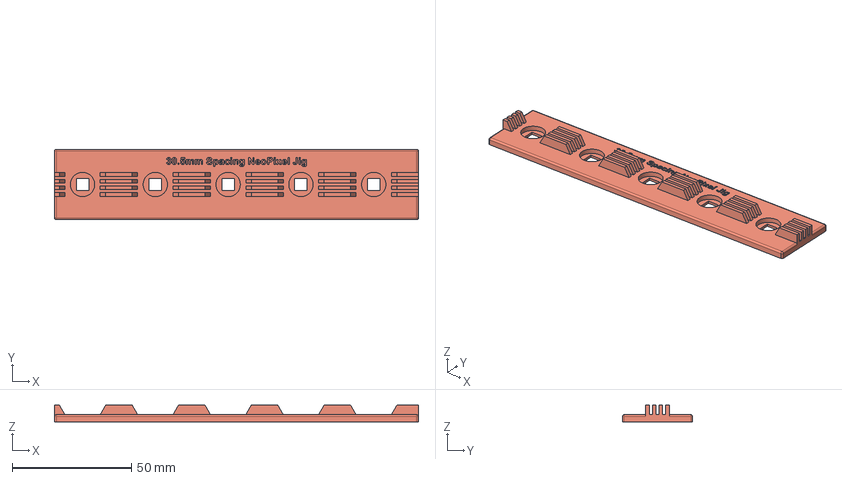
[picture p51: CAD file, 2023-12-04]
Recommended_Options/ERCT_Buffer/CAD/STEP/Tools/LED_Soldering_Tool.step
152.5 x 29.5 x 7.00 mm

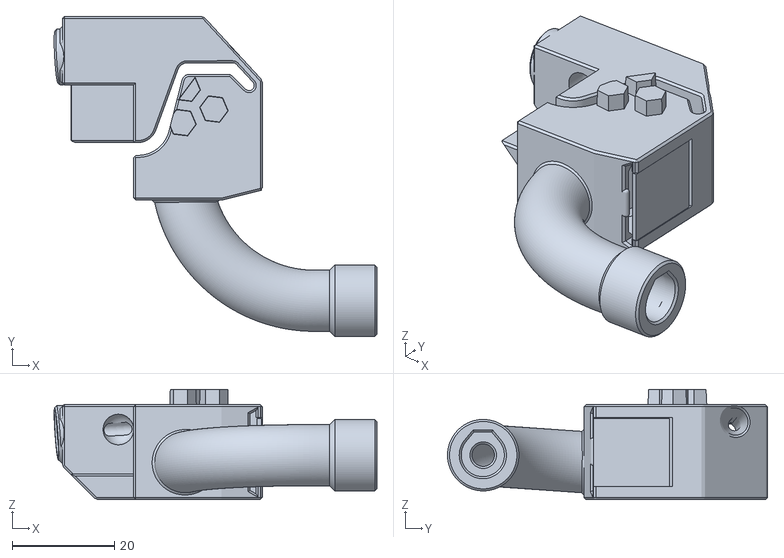
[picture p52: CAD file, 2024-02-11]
Recommended_Options/ERCT_Buffer/Options/180_Degree_Build/Coupler_Block/[a]_Coupler_Block_180_xN.stl
63.2 x 62.7 x 21.6

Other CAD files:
_Errata/Encoder_with_Status_LED/V623ZZ_Bearing/Encoder_Left_V623ZZ_Exit_LED_insert.stl
Recommended_Options/ERCT_Buffer/Options/180_Degree_Build/Support_Arms/[a]_Magnetic_PTEF_Coupler_B.stl
Recommended_Options/ERCT_Buffer/Stls/Axle/Axle_10_Double_Thread.stl
Recommended_Options/ERCT_Buffer/Stls/Coupler Block/[a]_Coupler_Block_xN.stl
CAD/Misc/Apron_Neopixels/ERCF Carrot on a Stick v2.f3d
CAD/Misc/Apron_Neopixels/LED_Soldering_Tool.f3d
CAD/Misc/Apron_Neopixels/LED_Soldering_Tool_24mm.f3d
CAD/Misc/Apron_Neopixels/Neopixel_Apron_Led_Holder.step
CAD/Misc/Apron_Neopixels/Neopixel_apron_PCB_Led_Holder.step
CAD/Misc/Calib_Test_redux.step
CAD/Misc/Encoder_v23.step
CAD/Misc/Filament_Block_Bearing_Insert_Tool.f3d
CAD/Misc/Filament_Block_Bearing_Insert_Tool.step
CAD/Misc/NEMA17_Tool_v2.step
CAD/Misc/PTFE_Tool.f3d
CAD/Misc/[a]_ERCF_Easy_Brd_Bracket_Bottom_Mount_With_Cable_Path.step
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

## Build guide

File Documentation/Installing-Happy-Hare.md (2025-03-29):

*\[This page has been taken from the Happy Hare Wiki (Thanks Moggie!) and modified to be specific to ERCF v2.\]*

#### Page Sections:
- [Cloning Happy Hare Repo](#---cloning-happy-hare-repo)
- [Running Installer](#---running-installer)
- [Creating Base Klipper Config](#---creating-base-klipper-config)
- [Pause/Resume/Cancel_Print Macros](#---pauseresumecancel_print-macros)
- [Upgrading](#---upgrading)

*\[This guide is copied directly from the [Happy Hare Installation](https://github.com/moggieuk/Happy-Hare/wiki/Installation) page. Thanks Moggie!\]*

This section deals with installing Happy Hare to the host computer (most commonly the Raspberry Pi). Basically, the installation proceeds as with any other git based software, indeed like Klipper itsself.

Happy Hare consists of a set of Klipper "extra" modules, a moonraker "component" and a set of macros and configuration files. To install you must first clone from Github and then install using the supplied install script. This install will both setup a base set of klipper configuration files as well as creating the symlinks necessary to link the cloned files into your Klipper/Moonraker installation.

Once installed it will be added to Moonraker update-manager for easy updates like other Klipper plugins.

<br>
 
## #f03c15 #c5f015 #1589F0 Cloning Happy Hare Repo

The first step is to clone the Happy Hare repository onto your Raspberry Pi. If you're unfamiliar with cloning, it just copies all the data in the git repository to your local computer. Since the Happy Hare git has all the necessay software, we use the `git clone` functionality to pull everything from github to the local computer (the rpi, in most cases of Klipper). So, go ahead and log into your rpi via ssh.

In power shell, and with Mainsail, this will look like this:  

```yml
ssh pi@mainsailos.local
```  

> [!NOTE]  
> You will notice in the following pictures the bash prompt is `Miriax@VoronRed:~`. Yours won't look like that. It will be `username@<hostname.:~` where the hostname is likely "mainsailos" or the ip address.

Alternatively, you can use your Klipper ip address, which will look something like this:  
```
ssh username@192.168.0.256
```  
(You'll need to change the username and ip address.)  

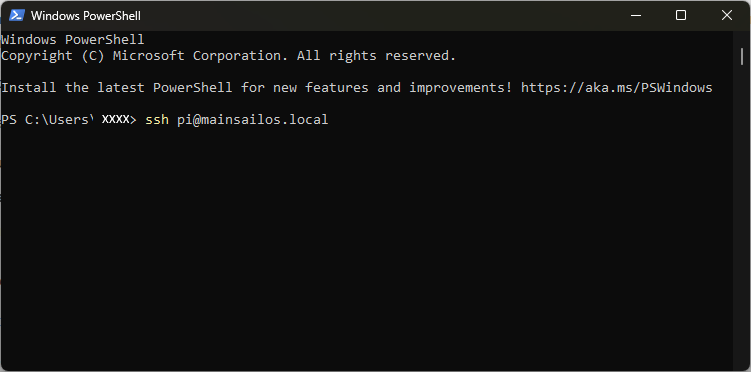
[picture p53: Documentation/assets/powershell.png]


From there, you're going to clone Happy Hare software to your rpi:  

```yml
cd ~
git clone https://github.com/moggieuk/Happy-Hare.git
```

(it's ok to click the copy icon and right click in the ssh terminal to paste or just type it out if you want.)  
Let that finish. It should only take a few seconds, and you'll now have your very own copy of Happy Hare stored on your rpi!
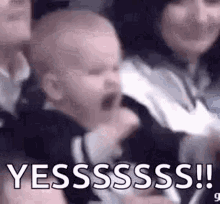
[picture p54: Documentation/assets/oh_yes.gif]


Now, you're going to change to the Happy Hare directory using the `cd` command (`cd` is Linux Geek for "change directory"):  

```yml
cd Happy-Hare
```

Here is a picture of the previous steps successfully performed:
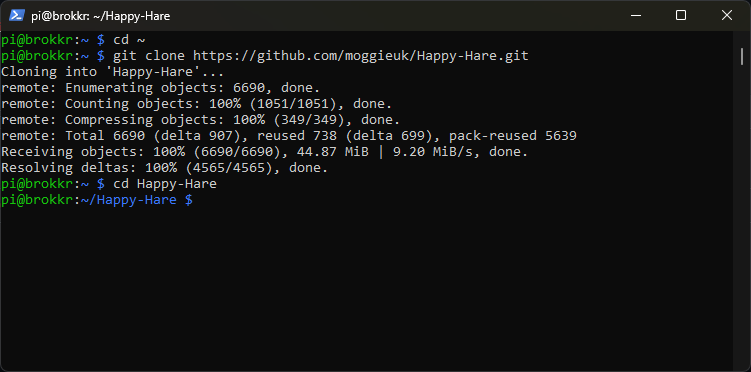
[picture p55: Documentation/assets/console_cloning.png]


<br>
 
## #f03c15 #c5f015 #1589F0 Running Installer

The install does not ship a set of template config files, instead you can create your starting templates by running the installer in interactive mode. This will ask questions that will be used to generate and install the template config. See [next section](#---creating-base-klipper-config). Read this section to familiarize yourself with command line options and determine if you need to use `-c`, `-k` or `-r` flags.

You'll be asked to run:

```
cd ~/Happy-Hare
./install.sh -i
```

The `-i` option will bring up an interactive installer to aid setting some confusing parameters. For popular external mcu boards it will also configure all the pins for you. If run without with the `-i` flag it defaults to updating the current installation which is sometimes necessary for significant version updates (see [here](Upgrade-Notice)). Note that if an existing install is found it will never be overwritten, it will be moved to a numbered backup folder with a `<file>.<date>` extension and current configuration defaults carried over. If you still choose not to install the new `mmu*.cfg` files automatically you can copy the templates and fill in all the tokens and blank parameters by hand. Frankly it is much easier to run through an initial install and use the generated config files as a starting point.
<br>

Note that the installer will look for Klipper install and config in standard locations. If you have customized locations or multiple Klipper instances on the same rpi, or the installer fails to find Klipper you can use the `-k` and `-c` flags to override the Klipper home directory and Klipper config directory respectively. Also, if installing on Repetier-Server add the `-r` option. E.g.
```
./install.sh -k /opt/klipper/LK5_Pro_ERCF -c /var/lib/Repetier-Server/database/klipper -m /opt/klipper/LK5_Pro_ERCF/moonraker -r LK5_Pro_ERCF -i
```

If you have multiple Klipper instances installed with for example Kiauh. You can use the `-a` flag to specify the service name. E.g.
```
./install-sh -a klipper-two -k <klipper_home_dir> -c <klipper_config_dir>
```

<br>

> [!IMPORTANT]  
> `mmu.cfg`, `mmu_hardware.cfg`, `mmu_macro_vars.cfg` & `mmu_parameters.cfg` (and other base config files) must all be referenced by your `printer.cfg` master config file with `mmu.cfg` and `mmu_hardware.cfg` listed first (the recommended way to achieve this is simply with `[include mmu/base/*.cfg]`). `mmu/optional/client_macros.cfg` should also explicitly be referenced if you don't already have working PAUSE / RESUME / CANCEL\_PRINT macros (but be sure to read the section beforehand regarding macro expectations and review the default macros). The install script can also include these optional config files for you.
<br>

> [!TIP]  
> If you are concerned about running `install.sh -i` then run like this: `install.sh -i -c /tmp -k /tmp` This will build the `*.cfg` files for you but put then in /tmp rather than overwriting your active configuration. You can then refer to them, pulling out the bits you need to augment your existing install or simply see what answers to the various questions will do...

```
Usage: ./install.sh [-a <kiauh_alternate_klipper>] [-k <klipper_home_dir>] [-c <klipper_config_dir>] [-m <moonraker_home_dir>] [-b <branch>] [-r <repetier_server stub>] [-i] [-d] [-z]

-i for interactive install
-d for uninstall
-b to switch to specified feature branch (sticky)
-z skip github check (nullifies -b <branch>)
-r specify Repetier-Server <stub> to override printer.cfg and klipper.service names
-a <name> to specify alternative klipper-service-name when installed with Kiauh.
-c <dir> to specify location of non-default klipper config directory
-k <dir> to specify location of non-default klipper home directory
(no flags for safe re-install / upgrade)
```

<br>
 
## #f03c15 #c5f015 #1589F0 Creating Base Klipper Config

### Running the installation script
Finally, you'll install Happy Hare using a bash script which contains all the commands necessary to install Happy Hare:  

```
./install.sh -i
```  

> [!NOTE]  
> Here, we're using the `-i` switch (switch is more Linux Geek for "option") to activate an interactive install. This will help guide you through setting most basic options for your MMU. This is generally only needed for the first install. Upgrading can be done by `./install.sh` with no switches.

You'll be asked a series of questions pertaining to your hardware and options.

### 1.  MMU Type
Choose ERCFv2.0 from the list.

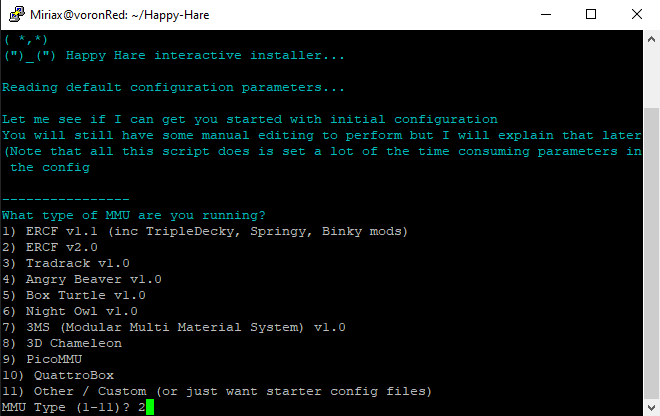
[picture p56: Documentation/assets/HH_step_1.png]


### 2. Number of Gates
Happy Hare installer then asks for the number of gates.  

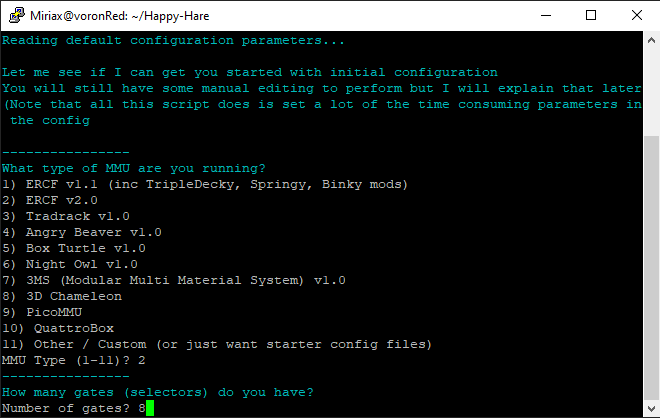
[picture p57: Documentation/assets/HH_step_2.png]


Enter the correct number of gates for your ERCF, usually 8 in v2.5.

#### 3. Control Board
Select the type of control board you have installed. MMBv1.1 and MMBv2.0 are the recommended boards for ERCFv2.

*\[This graphic will be updated soon\]*

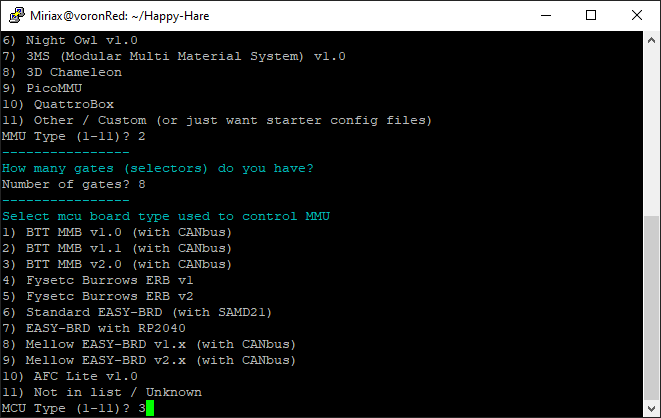
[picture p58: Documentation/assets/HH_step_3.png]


#### 4. Control Board Address
Happy Hare will then attempt to figure out where your control board is. So far, this doesn't work for CANBUS boards. If your printer's mainboard is connected, that will be detected instead, so input "N," unless you're using a Remote MCU setup.

> [!NOTE]
> If you followed the previous guide on [Flashing Your Local MCU](https://github.com/Enraged-Rabbit-Community/ERCF_v2/blob/master/Documentation/Flashing-Local-MCU.md), you should already know your CANBus UUID. You will need to manually add the CANBus UUID to the top of your mmu.cfg. If you are using USB instead, this should work and find your board!

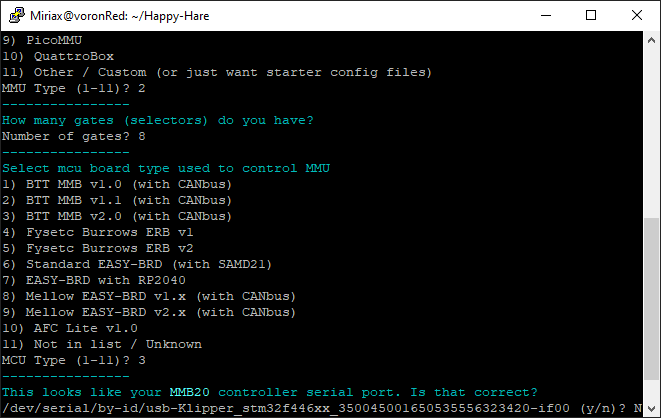
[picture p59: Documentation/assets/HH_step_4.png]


#### 5. LED Options
If you have neopixels installed on your ERCF, enable them here.  

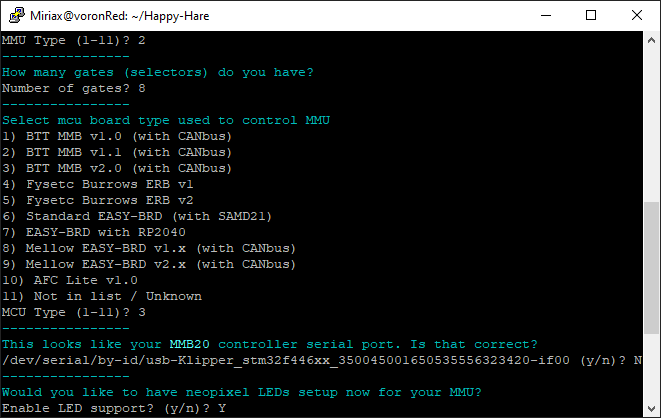
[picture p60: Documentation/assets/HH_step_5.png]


#### 6. Selector Touch Operation
Decide whether or not to enable Selector Touch operation. This can help with recovery of an error, but is also a bit difficult to get set up properly. It's better to say "no" and get it working after you're more familiar with the ERCF and Happy Hare.

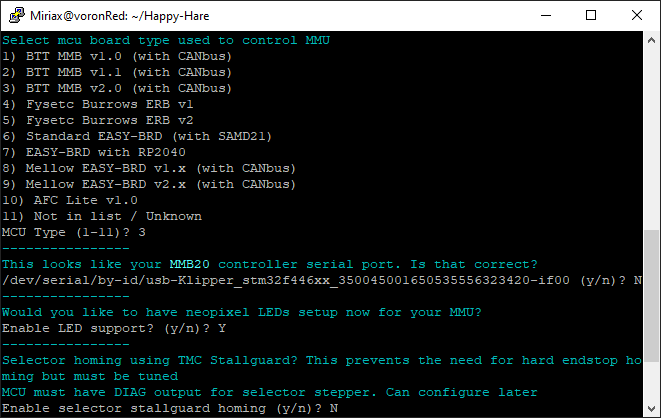
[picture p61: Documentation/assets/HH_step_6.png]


#### 7. Servo Options
Select your servo option from the list.

> [!NOTE] 
> You're going to adjust the angles later, so this doesn't matter too much right now. During Beta Testing, this is something we'll ask you to report on so that we can make more accurate presets.

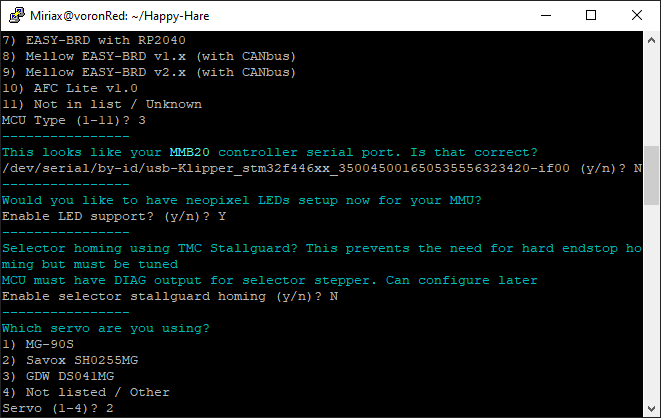
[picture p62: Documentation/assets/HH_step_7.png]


#### 8. Clog detection
With Binky, It's probably best to enable clog detection and set it to automatic. This acts like a smart filament sensor and will pause the print if something goes bad with the filament feed.  

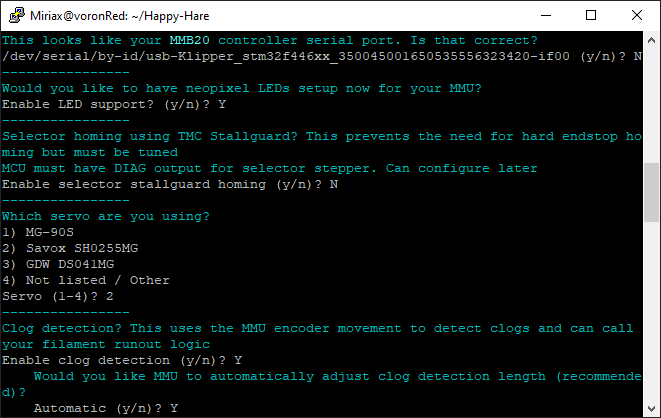
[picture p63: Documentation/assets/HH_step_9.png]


#### 9. EndlessSpool
Happy Hare has the capability to map multiple gates to one tool. This allows for "endless spool" operation. When one spool runs out, if you have the same material and color mapped to another gate, it will automatically switch to the other gate and resume printing. This option is recommended for long prints.

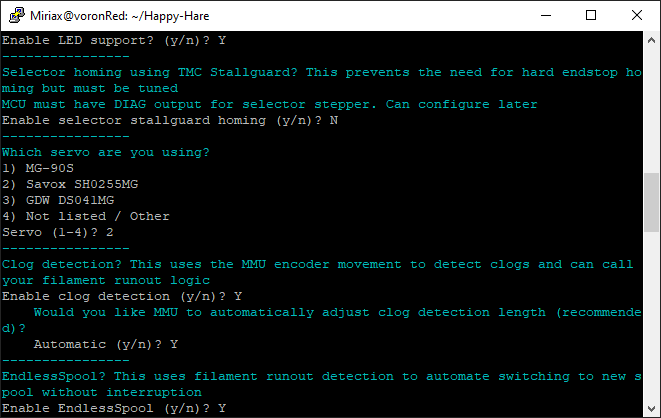
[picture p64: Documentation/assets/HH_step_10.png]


#### 10. Final step
The last step asks to add the `[include mmu*]` lines to your printer.cfg. **On initial setup it is recommended to select yes.** If Happy Hare has already been installed, you should select "no."

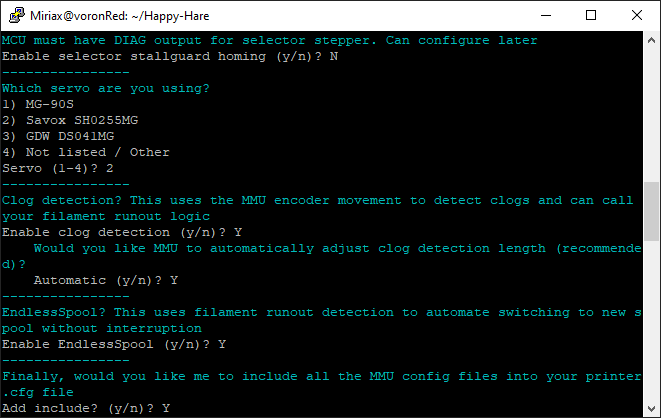
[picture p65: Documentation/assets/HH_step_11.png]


From here, Happy Hare will install itself with the options you've selected. You should have a nice little report that Happy Hare is ready:  

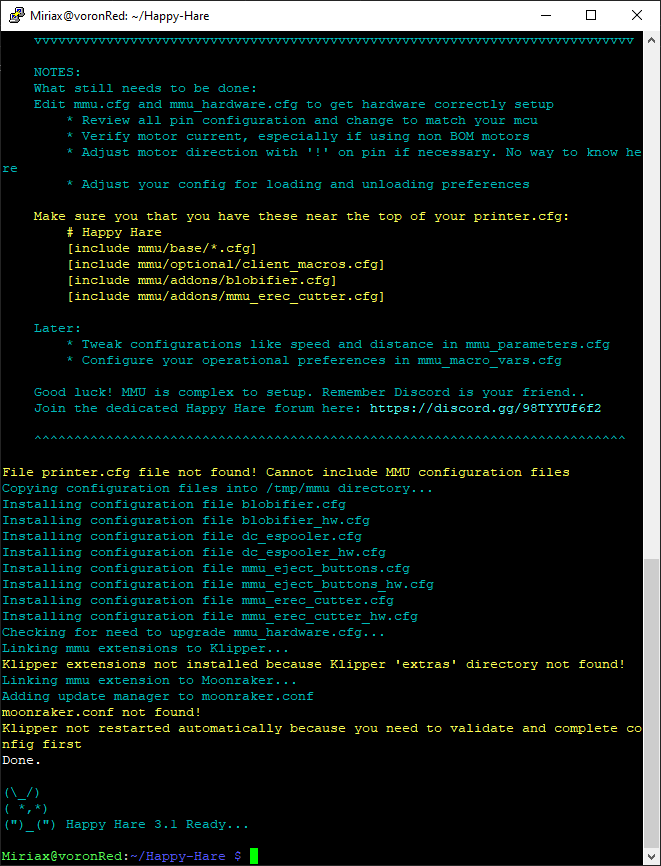
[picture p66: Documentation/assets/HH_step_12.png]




> [!NOTE] 
> During Beta testing, and really any time it happens, **please report any misfires by the automatic setup!**

Once this has been run sucessfully you will have outline configuration files installed. Happy Hare creates a hierachy of files in the klipper config directory. To review the layout and purpose of each of these files read [Configuration Reference](https://github.com/moggieuk/Happy-Hare/wiki/Configuration-Reference)

Now, you have Happy Hare installed on your rpi. Feels good, doesn't it?  
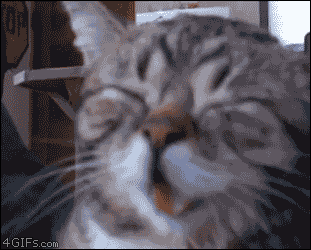
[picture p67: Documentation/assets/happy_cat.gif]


<br>

## #f03c15 #c5f015 #1589F0 Pause/Resume/Cancel\_Print Macros

It is recommended that you use the PAUSE/RESUME/CANCEL\_PRINT macros aka "client macros" that are supplied with Happy Hare at least when setting up. The reason is that they are reasonably full featured and integrate with the "sequence" macros you will learn about later that control toolhead movement during a toolchange. These macros can be used by ensuring that this appears in your `printer.cfg` config after the `[include mmu/base/*.cfg]`:

> [include mmu/optional/client\_macros.cfg]

Regardless of whether you use your own or use the ones provided in `client_macros.cfg`, Happy Hare will automatically wrap anything defined so that it can inject the essential steps to control the MMU.

During a print, if Happy Hare detects a problem, it will record the print position, safely lift the nozzle up to `z_hop_height_error` at `z_hop_speed` (to prevent a blob). It will then call the user's PAUSE macro (which can be the example one supplied in `mmu_software.cfg`). As can be seen with the provided examples it is expected that pause will save it's starting position (GCODE\_SAVE\_STATE) and move the toolhead to a park area, often above a purge bucket, at fast speed.

The user then addresses the issue and calls `RESUME` to continue with the print. More on that subject can be found in Happy Hare's [Handling Errors](https://github.com/moggieuk/Happy-Hare/wiki/Handling-Errors).

The user's RESUME macro may do some purging or nozzle cleaning but is expected to return the toolhead to where it was left when the pause macro was called. At this point the Happy Hare wrapper takes over and is responsible for dropping the toolhead back down to the print and resumes printing.

Happy Hare will always return the toolhead to the correct position, but if you leave it in your park area will will move it back very slowly. You can to follow the above sequence to make this operation fast to prevent oozing from leaking on your print.

<br>

## #f03c15 #c5f015 #1589F0 Upgrading

Happy Hare is always being improved. You can update in the same way as you update Klipper through the update-manager facility in Moonraker when update is indicated. If you know an update is pending and it is not yet shown in update-manager (it can take 24h) you can force a refresh by clicking on the circular arrow.

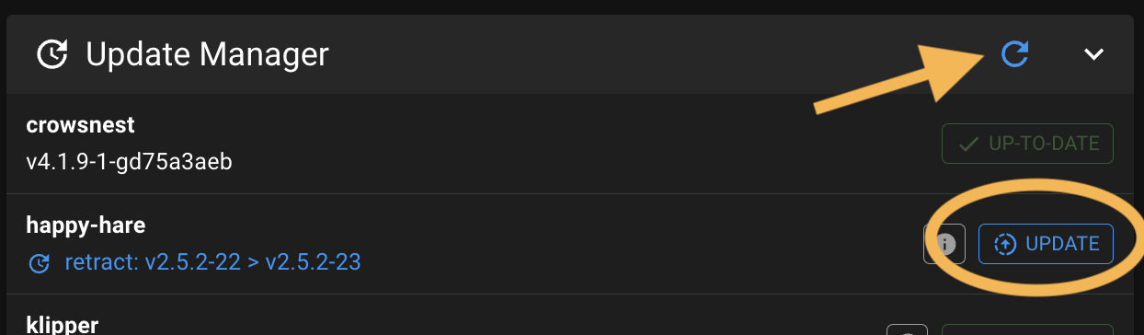
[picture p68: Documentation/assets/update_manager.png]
<p align="center"><p>

Sometimes an update includes a major change and simply upgrading through update manager is not sufficent. When this occurs you should see an error message directing you to the [Upgrade Notice](https://github.com/moggieuk/Happy-Hare/wiki/Upgrade-Notice) page (read that now because it explains major/minor/point release conventions). You will then need to run the `install.sh` script as below.

Alternatively you can simply run the following. Note that you **must not add the `-i` option to update**. This will pull the very latest code from Github and upgrade any necessary configuration files. This is also a good option to run if you suspect you have broken something or you have upgraded Klipper and it has removed the Happy Hare added modules (Hint: If you see a "step pin not defined for..." it is highly lightly that klipper has lost the Happy Hare modules and it struggling to parse the config).

```yml
cd ~/Happy-Hare
./install.sh
```

> [!TIP]  
> Don't be shy about running this. If there is nothing to update the script will do nothing and it will always backup your entire config in a directory [see config file structure](https://github.com/moggieuk/Happy-Hare/wiki/Configuration-Reference#---location-of-configuration-files) in a parallel directory with name with date stamp, similar to `mmu-20240422_102329`. The new `mmu` directory will be rebuilt extracting all the previous configuration but with updated templates. Note that an additional backup directory is created each time you run the installer uniquely date stamped.

> [!IMPORTANT]  
> If you have Klipper installed in a non-default location (i.e. you used the `-c`,`-k` or `-r` flags) you will need to add these flags again to the above, otherwise the upgrade will look in the default location and likely not find/upgrade what you expect.

### ERCF Setup Steps:
- [Flashing Your Local MCU](https://github.com/Enraged-Rabbit-Community/ERCF_v2/blob/master/Documentation/Flashing-Local-MCU.md)
- Installing Happy Hare
- [Happy Hare Configuration](https://github.com/Enraged-Rabbit-Community/ERCF_v2/blob/master/Documentation/Happy-Hare-Configuration.md)
- [Hardware Configuration Checks](https://github.com/Enraged-Rabbit-Community/ERCF_v2/blob/master/Documentation/Hardware-configuration-checks.md)
- [Hardware Calibration](https://github.com/Enraged-Rabbit-Community/ERCF_v2/blob/master/Documentation/Hardware-Calibration.md)
- [Toolhead Distances](https://github.com/Enraged-Rabbit-Community/ERCF_v2/blob/master/Documentation/Toolhead-Distances.md)
- [Installing KlipperScreen Happy Hare](https://github.com/Enraged-Rabbit-Community/ERCF_v2/blob/master/Documentation/Installing-KlipperScreen.md)
- [Slicer Setup](https://github.com/Enraged-Rabbit-Community/ERCF_v2/blob/master/Documentation/Slicer-Setup.md)
- [Further Mods to Consider](https://github.com/Enraged-Rabbit-Community/ERCF_v2/blob/master/Documentation/Further-Mods.md)

#### Even more Happy Hare info can be found at:
- [Happy Hare Wiki](https://github.com/moggieuk/Happy-Hare/wiki)

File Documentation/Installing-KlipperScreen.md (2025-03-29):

#### Page Sections:
  - [Installation](#---installation)
  - [Caveats & Possible problems / workarounds](#---caveats--possible-problems--workarounds)
  - [Font Problems](#---font-problems)
  - [Blank Screen After Update](#---blank-screen-after-system-update)
  - [Happy Hare Version Incompatibility](#---happy-hare-version-incompatibility)
  
*\[This guide is copied from the [KlipperScreen Happy Hare repo](https://github.com/moggieuk/KlipperScreen-Happy-Hare-Edition) and reformatted for ERCF. Thanks Moggie!\]*

## #f03c15 #c5f015 #1589F0 Installation
**Firstly, make sure Happy Hare software is completely up-to-date. Features were added to support this KlipperScreen add on.**

Install and setup a base KlipperScreen from the original source. Get it working. Don't skip this step because we cannot help with basic KlipperScreen and system setup.  Once you have that installed and working, log into you Rasberry Pi and execute the following commands. You can cut'n'paste...

    cd ~
    mv KlipperScreen KlipperScreen.orig
    git clone https://github.com/moggieuk/KlipperScreen-Happy-Hare-Edition.git KlipperScreen
   
    cd ~/KlipperScreen/happy_hare
    ./install_ks.sh -g <num_gates>
   
(where <num_gates> is the number of selectors you built with, e.g. 8 for a typical ERCF v2)
   
KlipperScreen will be restarted and hopefully you should now be running the enhanced version!

> [!NOTE]  
> Expert Tip: The last step of running './install_ks -g <num_gates>' can be run many times.. and sometimes is needed after an update to install new images or update menu structure. If you customize the MMU part of the KlipperScreen menu and want to make use of the "replicator" function that will automatically replicate menu options for the configured number of gates, you can edit menus.conf and reference the templating there.

Note that the base KlipperScreen is up-to-date (and Moggieuk will continue to merge with master every 2 weeks) with changes in the original but also includes extra menu functionality that can be used in the creation of your custom menus.  See the generated ercf_klipperscreen.conf for clues!

## #f03c15 #c5f015 #1589F0 Caveats & Possible problems / workarounds
I have only tested on a single screen.  A 640x480 resolution BTT TFT5.0.   It is possible that you might find layout problems on other (likely smaller) displays.  Also, I have only tested in and optimized for horizonal orientation.  I doubt it will be effective in vertical but I don't know of any Voron owners with vertically mounted panels.

JFYI the installer will alter or add the KlipperScreen entry in `moonraker.conf`:

    [update_manager KlipperScreen]
    type: git_repo
    path: ~/KlipperScreen
    origin: https://github.com/moggieuk/KlipperScreen-Happy-Hare-Edition.git
    env: ~/.KlipperScreen-env/bin/python
    requirements: scripts/KlipperScreen-requirements.txt
    install_script: scripts/KlipperScreen-install.sh
    managed_services: KlipperScreen

## #f03c15 #c5f015 #1589F0 Font problems:
The CSS style only specifies a "Free Mono" font to be used (the same as original KlipperScreen) for all textual displays.  I use the Unicode Box character set in that font to render the selector status, filament positions and TTG map. A couple of users have reported issues with this part of the display, either not appearing or not spaced correctly.  E.g.

mmu_panel_printing

If this occurs the first thing to try is to run the following, then restart KlipperScreen:

    sudo apt install fontconfig
    fc-cache -f -v
    sudo systemctl restart KlipperScreen

If this doesn't fix the problem I suggest installing a new font set.

> [!NOTE]  
> A very useful way of listing the fonts you have installed on your system by family is with:
> > fc-list : family | sort | uniq

<details>
<summary>🔹 How to install JetBrains fonts...</summary>

Download the JetBrains fonts from (www.jetbrains.com).  Extract the zip.  Copy all the `*.ttf` fonts (you will find them under fonts/ttf in the extracted zip) into `/usr/share/fonts/truetype` directory (you will have to sudo cp else you will likely get permission denied), then cache these fonts:

    cd <path where you extracted the font files>/fonts/ttf
    sudo cp *.ttf /usr/share/fonts/truetype
    fc-cache -f -v
     
Then finally update the font reference in the KlipperScreen css file:

    cd ~/KlipperScreen/styles

Edit the `base.css` file.  Find the css entry for `.mmu_status`, then change the font-family to:

    font-family:      JetBrains Mono;

(by default it is `font-family:     Free Mono;`)

Then restart KlipperScreen

    sudo systemctl restart KlipperScreen

If you have to do this, please let Moggieuk know the details about the operating system you are running on and how you installed KlipperScreen in the first place... if I can locate the source of the issue I might be able to workaround in the future.

</details>

## #f03c15 #c5f015 #1589F0 Blank Screen after system update
It has come to my attention that sometimes a system (OS) update can break KlipperScreen.  This is nothing to do with KlipperScreen but rather the installation of a slightly broken video driver `fbturbo`.  Luckily the fix is simple.  After OS upgrade run:

    sudo apt purge xserver-xorg-video-fbturbo

## #f03c15 #c5f015 #1589F0 Happy Hare version incompatibility
If you are upgrading and see a message like this when accessing the main MMU panel it is probably because of a version mismatch with Happy Hare on your printer.  Follow the instructions in the popup!



*All screen shots are taken with the "Colorize" theme (my preference because the buttons are more defined).  The default is z-bolt and looks slightly different.*

### ERCF Setup Steps:
- [Flashing Your Local MCU](https://github.com/Enraged-Rabbit-Community/ERCF_v2/blob/master/Documentation/Flashing-Local-MCU.md)
- [Installing Happy Hare](https://github.com/Enraged-Rabbit-Community/ERCF_v2/blob/master/Documentation/Installing-Happy-Hare.md)
- [Happy Hare Configuration](https://github.com/Enraged-Rabbit-Community/ERCF_v2/blob/master/Documentation/Happy-Hare-Configuration.md)
- [Hardware Configuration Checks](https://github.com/Enraged-Rabbit-Community/ERCF_v2/blob/master/Documentation/Hardware-configuration-checks.md)
- [Hardware Calibration](https://github.com/Enraged-Rabbit-Community/ERCF_v2/blob/master/Documentation/Hardware-Calibration.md)
- [Toolhead Distances](https://github.com/Enraged-Rabbit-Community/ERCF_v2/blob/master/Documentation/Toolhead-Distances.md)
- Installing KlipperScreen Happy Hare
- [Slicer Setup](https://github.com/Enraged-Rabbit-Community/ERCF_v2/blob/master/Documentation/Slicer-Setup.md)
- [Further Mods to Consider](https://github.com/Enraged-Rabbit-Community/ERCF_v2/blob/master/Documentation/Further-Mods.md)

#### Even more Happy Hare info can be found at:
- [Happy Hare Wiki](https://github.com/moggieuk/Happy-Hare/wiki)

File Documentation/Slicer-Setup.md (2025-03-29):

#### Page Sections:
- [Start G-Code](#---start-g-code)
- [End G-Code](#---end-g-code)
- [Toolchange G-Code](#---tool-change-g-code)
- [Customizing MMU Start/End Macros](#---customing-mmu-startend-macros)
- [MMU Error Dialog](#---mmu-error-dialog)
- [Slicer Tip Forming](#---slicer-tip-forming)
  - [Turning off slicer tip forming](#turning-off-slicer-tip-forming)
  - [Turning off slicer wipetower](#turning-off-slicer-wipetower)
  - [How to verify configuration](#how-to-verify-configuration)

*\[This guide is copied directly from the [Happy Hare Slicer Setup](https://github.com/moggieuk/Happy-Hare/wiki/Slicer-Setup) page. Thanks Moggie!\]*

When printing with an MMU you must augment the gcode generated by your slicer to include logic to initialize the MMU, load the initial filament and optionally reset and eject filament at the end of the print. To achive that it is necessary to enable MMU support in your slicer and then edit the custom g-code. While there are many ways to do this, Happy Hare recommends the following pre-packaged macro to take advantage of all the advanced features. Consider this best practice for setut and note the probable need to separate your existing "start_print" macro into two parts.

Make sure the `Expert Options` of your slicer are enabled and go to the Printer Settings tab.

<br>

## #f03c15 #c5f015 #1589F0 Start G-Code

Enter the following (using your own print start macro call) into your "custom start g-code" box:

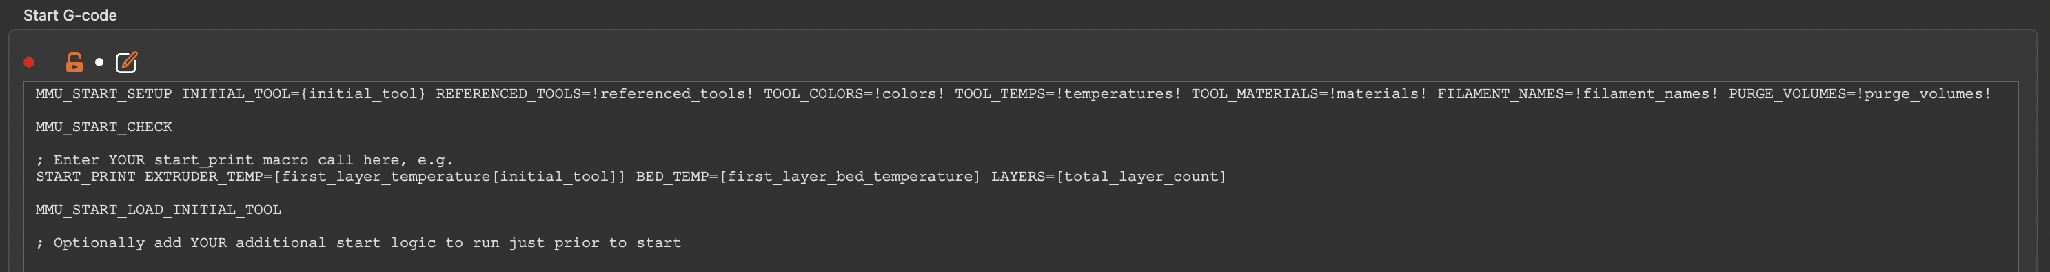
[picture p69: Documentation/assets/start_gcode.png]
Custom Start G-Code
<br>Your `START_PRINT ...` macro is likely to be different from mine! Here is some cut'n'paste text:

```yml
MMU_START_SETUP INITIAL_TOOL={initial_tool} TOTAL_TOOLCHANGES=!total_toolchanges! REFERENCED_TOOLS=!referenced_tools! TOOL_COLORS=!colors! TOOL_TEMPS=!temperatures! TOOL_MATERIALS=!materials! FILAMENT_NAMES=!filament_names! PURGE_VOLUMES=!purge_volumes!
MMU_START_CHECK
; Enter YOUR exist start_print macro call here (minus purging logic because tool may not be loaded yet)
MMU_START_LOAD_INITIAL_TOOL
; Optionally add YOUR additional start logic (like purging) here to run just prior to start
SET_PRINT_STATS_INFO TOTAL_LAYER={total_layer_count} ; For pause at layer functionality and better print stats
```

> [!NOTE]  
> There are two reasons that it is recommended to add these separate 4-5 lines in your slicer:<br>
> - Keeping them as separate gcode macros to enables the print to pause and then continue in the case of an error.  If you bundle everything into a single print start macro then the first opportunity to pause will be at the end of that, potentially long running, macro! (This is particularly accute if using the new klipper pop-up dialogs -- these frustratingly will not be able to be closed until the current macro is complete)
> - You will likely want to separate out any nozzle purging logic you have in your current "start_print" marco and run it AFTER all the MMU checks and loading the initial tool

### Sequence Explained:

#### `1. MMU_START_SETUP`
This is a macro (defined in `mmu_software.cfg`) that is passed information either through slicer "placeholder" variables delimited by `{}` like `{initial_tool}` or through a similar mechanism implemented by Happy Hare's moonraker extension which pre-processes the g-code file when it is uploaded and substitutes `!!` like `!referenced_tools!` that are useful for MMU printing. Unfortunately these placeholders are absent in all popular slicer programs hence the pre-processor extension. Happy Hare's g-code pre-processing is explained in [detail here](https://github.com/moggieuk/Happy-Hare/wiki/Gcode-Preprocessing)

This macro initializes the MMU, establishes whether the print is single or multi-color, detects when the intent is to print bypassing the MMU and then stores this infomation in Happy Hare for the duration of the print in the "Slicer Tool Map". This can be accessed in your own macros through the `printer.mmu.slicer_tool_map` printer variable. E.g.

```yml
   printer.mmu.slicer_tool_map.
      initial_tool: 0          ; Initial tool number expected to be loaded at the beginning of the print
      ; List of all the tools referenced in the print (T0 and T3)
      tools.0.color: ff0000    ; Color in RRGGBB format for T0
      tools.0.material: ABS    ; Material type for T0
      tools.0.temp: 240        ; Extruder temperature for T0
      tools.0.in_use: 1        ; Tool used in print
      tools.3.color: 00e410    ; Color in RRGGBB format for T3
      tools.3.material: ASA    ; Material type for T3
      tools.3.temp: 245        ; Extruder temperature for T3
      tools.3.in_use: 1        ; Tool used in print
      purge_volumes: [[100, 100], [100, 100]] ; NxN matrix of purge volume changing from tool X to tool Y
```

The "Slicer Tool Map" can be displayed on the console at any time during the print by running the `MMU_SLICER_TOOL_MAP` command without any set parameters (optional `DETAIL=1` or `PURGE_MAP=1` or `SPARSE_PURGE_MAP=1` to see purge matrix):<br>
> MMU_SLICER_TOOL_MAP PURGE_MAP=1<br>
```
-------- Slicer MMU Tool Summary ---------
2 color print (Purge volume map loaded)
T0 (Gate 0, ABS, ff0000, 240°C)
T3 (Gate 3, ASA, 00e410, 245°C)
Initial Tool: T0
-------------------------------------------
Purge Volume Map:
To -> T0   T1   T2   T3   T4   T5   T6   T7   T8
T0    -   200  200  200  200  200  200  200  200
T1   200   -   200  200  200  200  200  200  200
T2   200  200   -   200  200  200  200  200  200
T3   200  200  200   -   200  200  200  200  200
T4   200  200  200  200   -   200  200  200  200
T5   200  200  200  200  200   -   200  200  200
T6   200  200  200  200  200  200   -   200  200
T7   200  200  200  200  200  200  200   -   200
T8   200  200  200  200  200  200  200  200   -
```
Note that the `DETAIL=1` flag will also report on tools that are defined in slicer but not defined for current print. Similarly adding `SPARSE_PURGE_MAP=1` can make the purge volumes more readable but showing only referenced tools.

#### `2. MMU_START_CHECK`
This macro uses the "Slicer Tool Map" and performs checks to ensure the MMU is fully ready to print. Currently checks are limited to confirming that filament is available in all the required tools, but in the future it might check that the filaments types the sliced g-code expects match those actually loaded in the MMU (think how the Spoolman integration could be used...)
If this macro fails, the print will pause but not abort or skip the rest of the startup sequence. 

> [!TIP]  
> On failure while in a paused state, you can run this macro by hand to repeat the checks. Simply run `MMU_START_CHECK` without any parameters

#### `3.`START_PRINT...
This is where you put your normal print start macro passing additional slicer placeholders it may require. This macro doesn't need to do anything added for MMU support and will likely home the printer, level the bed and set print temperatures. It shouldn't have logic that assumes the extruder is loaded with filament - activities like purging should be separated out and included later (see step 5).

#### `4. MMU_START_LOAD_INITIAL_TOOL`
This macro will load the initial tool used by the print. No need to pass it any information - it retrieves it from the "Slicer Tool Map" setup earlier

#### `5.` Optional purge logic...
Optionally you can put the parts of your original print start macro that you separated out here. Typically this would be the logic that purges the nozzle, cleans nozzle and prints prime line. This is separated out because you want it to run AFTER the initial tool have been loaded.

<br>

> [!TIP]  
> Did you know the slicer defined extruder colors can be displayed on Mainsail / Fluidd UI next to the Extruder "Tx" buttons (see below). Happy Hare ensures the color information is parsed from the slicers g-code and provided to this user interface.
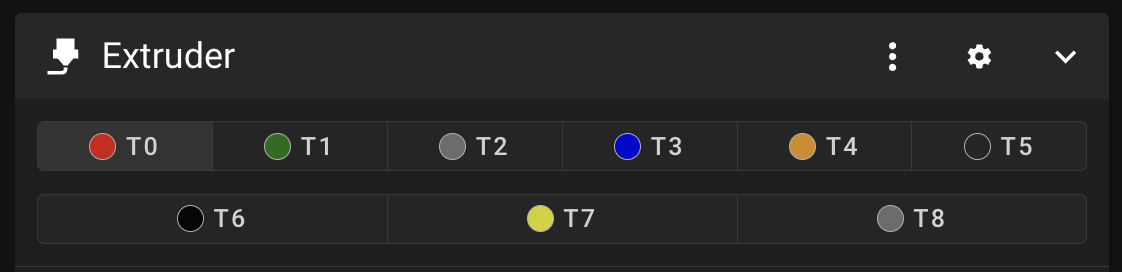
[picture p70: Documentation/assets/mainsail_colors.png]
Mailsail Extruder Colors
> 

<br>

## #f03c15 #c5f015 #1589F0 End G-Code

Ensure this is added in your slicer's "custom end g-code" box:

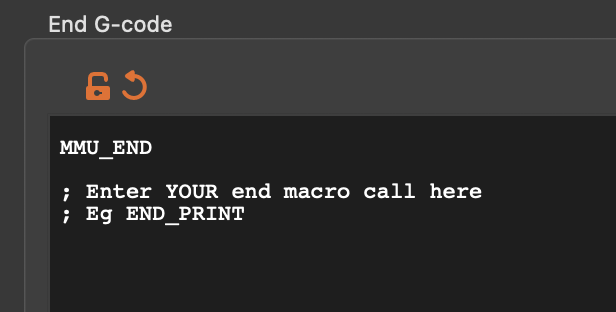
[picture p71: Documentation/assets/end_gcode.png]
End G-Code


```yml
MMU_END
; Optionally enter YOUR print end macro call here
MMU_PRINT_END ; Only required if using Octoprint
```

#### `1. MMU_END`
This is a macro (defined in `mmu_software.cfg`) that finalizes MMU, can print stats, reset any TTG map and eject filament. It is recommended to run this before your existing print end macro which is likely to disable heaters and turn motors off.

#### `2. END_PRINT`
This is where your existing print end macro would be placed

#### `3. MMU_PRINT_END`
This should be the very last g-code executed. When printing from virtual sd-card this isn't techincally necessary (and can be omitted) because Happy Hare will automatically detect the end of print. **It is necessary when printing from Octoprint.**

<br>

## #f03c15 #c5f015 #1589F0 After Layer Change G-Code

The reason for this is to support sequential printing and explained [here](https://github.com/moggieuk/Happy-Hare/wiki/Toolchange-Movement#---z-hop-moves)

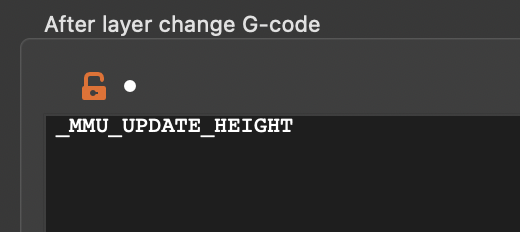
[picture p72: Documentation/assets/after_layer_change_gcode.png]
After Layer Change G-Code


```yml
_MMU_UPDATE_HEIGHT

; If you want enhanced pausing feature with Happy Hare client macros also add this
SET_PRINT_STATS_INFO CURRENT_LAYER={layer_num} ; For pause at layer functionality and better print stats
```

<br>

## #f03c15 #c5f015 #1589F0 Tool Change G-Code

This is likely to be the slicer default, but it is worth checking that the custom tool change g-code is set to this:

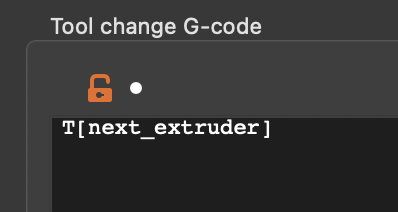
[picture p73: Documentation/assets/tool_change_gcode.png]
Tool Change G-Code


```yml
T[next_extruder]
```

<br>

## #f03c15 #c5f015 #1589F0 Customing MMU Start/End Macros

The recommended macro described here can be customized in `mmu_macro_vars.cfg`. Look for the `_MMU_SOFTWARE_VARS` section (corresponding to `mmu_software.cfg` where the macros are defined) 

```yml
# PRINT START/END ---------------------------------------------------------
#   (base/mmu_software.cfg)
#
[gcode_macro _MMU_SOFTWARE_VARS]
description: Happy Hare optional configuration for print start/end checks
gcode: # Leave empty

# These variables control the behavor of the optional _MMU_INITIALIZE and _MMU_LOAD_INITIAL_TOOL macros
variable_user_pre_initialize_extension      : "G28"     ; Executed at start of _MMU_INITIALIZE. Commonly G28 to home
variable_home_mmu                           : False     ; True/False, Whether to home mmu before print starts
variable_check_gates                        : True      ; True/False, Whether to check filament is loaded in all gates used
variable_load_initial_tool                  : True      ; True/False, Whether to automatically load initial tool

# These variables control the behavor of the optional _MMU_FINALIZE macro
variable_eject_tool                         : True      ; True/False, Whether to eject the tool at the end of the print
variable_reset_ttg                          : False     ; True/False, Whether reset TTG map at end of print
variable_dump_stats                         : True      ; True/False, Whether to display print stats at end of print
```

<br>

## #f03c15 #c5f015 #1589F0 MMU Error Dialog

When Happy Hare detects an error, even during print start it will pause the print allowing you to fix and then resume. If the option `show_error_dialog: 1` is set in `mmu_parameters.cfg` a pop-up dialog will be displayed on Mailsail/Fluidd/KlipperScreen providing you options through the UI. If it is occurs during these startup macros there will also be an option to abort the print. The abort option will disappear during the print. To disable the popup, set `show_error_dialog: 0`

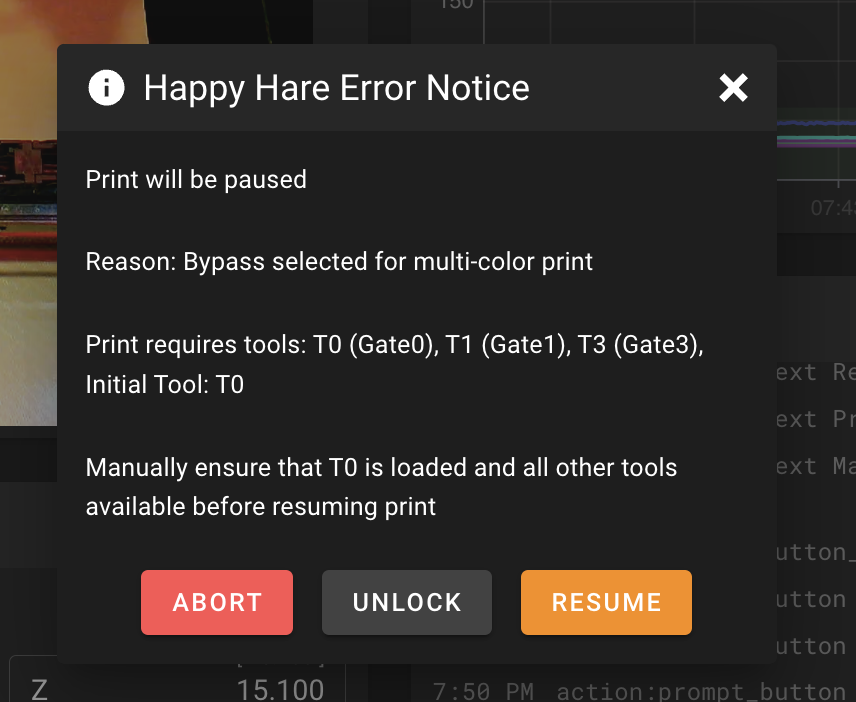
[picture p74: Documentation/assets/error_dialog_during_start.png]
Error Dialog


> [!IMPORTANT]  
> If you are writing your own startup macros beware of the earlier note because the use of a popup dialog can make it seem as though your printer is locked up for long running macros

<br>

## #f03c15 #c5f015 #1589F0 Slicer Tip Forming

The most important part of MMU printing is understanding how to configure your slicer for "single extruder multi material".  Because each slicer is different this is beyond the scope this documentation.  That said, the common slicers: Prusaslicer, Superslicer and Orcaslicer all have similar interfaces and there are a couple of settings you need to be aware of in deciding between what is performed by Happy Hare (the MMU "firmware") and the slicer.

### Turning off slicer tip forming
The first thing that has to happen on a tool change is to prepare the tip of the filament being removed from the extruder. The simplist and recommend approach is to disable the tip creation process in the slicer and allow Happy Hare to do this. The reason is Happy Hare will have to do this while not actively printing anyway - so why configure what will likely be the most furstrating part of your journey in two places.

Slicers have some quirks and don't make it very straighforward to turn off as you would expect. Instead you need to configure in a number of different areas.  This screenshots shown here are for Prusaslicer but Superslicer and Orcaslicer are very similar.

The first place is a setting like this on the `printer settings` tab.  This disables the primary retract/extrude oscillation that is the bulk of the tip forming and cooling movement.

> [!NOTE]  
> Whilst it is logical to zero all these settings out, Older versions of Prusaslicer (v2.5 - v2.7) at least has bug that will insert illegal `G1 F0` commands if all the fields are exactly 0.  For these versions only use a tiny value for the cooling tube length, like "0.01" instead.
> <br>
> **With PrusaSlicer v2.8 and above please use a value of exactly 0.**

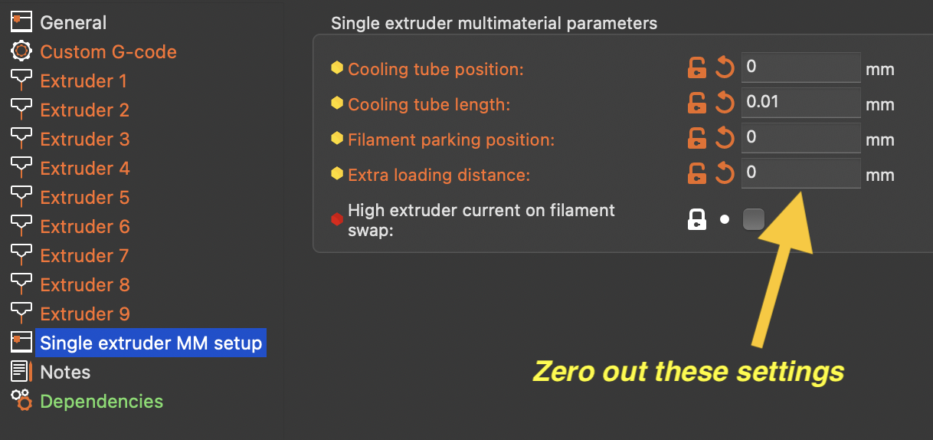
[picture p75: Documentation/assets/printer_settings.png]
Slicer printer settings


Working in conjunction with the above and found on the `filament settings` tab is this area where you should zero out all all movement speeds and distances.  Leave only the timing inputs that you can tune once you know the average loading and unloading time for your particular MMU.

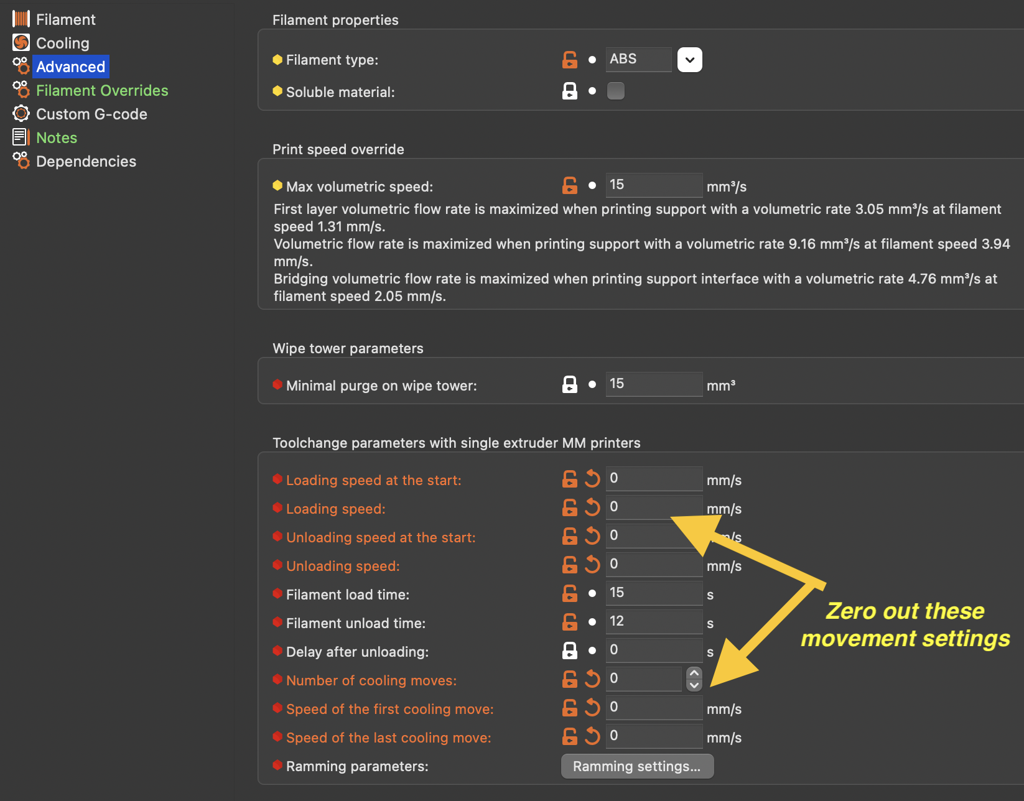
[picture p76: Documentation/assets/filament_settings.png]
Slicer filament settings


The next setting must be configure on each of your extruders.  This turns off an initial retraction and subsequent extrude that will leave blobs on your wipetower.  The reason to turn this off is that Happy Hare will correctly load the filament exatly to the nozzle and additonal extrusion will cause a blob.

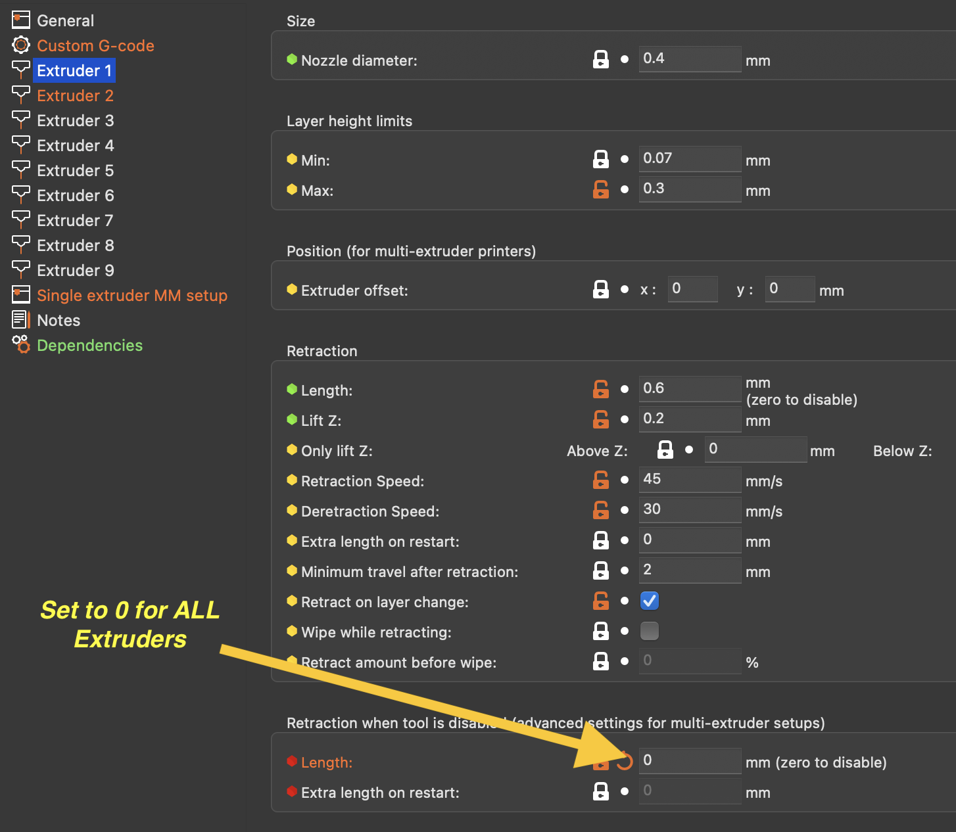
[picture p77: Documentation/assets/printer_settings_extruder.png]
Slicer printer settings per extruder


Unless you have a sepcialized purge system (documented later) you will want the slicer to manage a wipe tower used to purge out the remains of the previous filament.  To do this, make sure this option is enabled (it usually is by default):

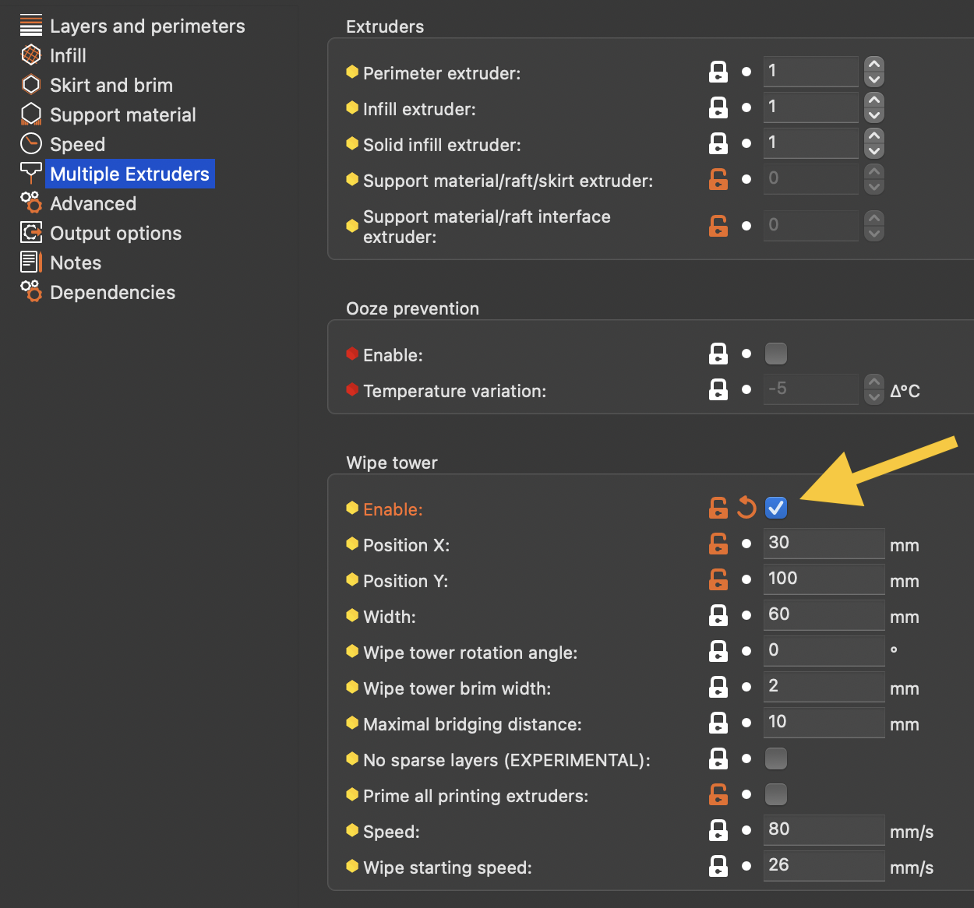
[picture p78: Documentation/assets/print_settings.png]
Slicer print settings


> [!NOTE]  
> If you use SuperSlicer, be sure to turn off Skinnydip:
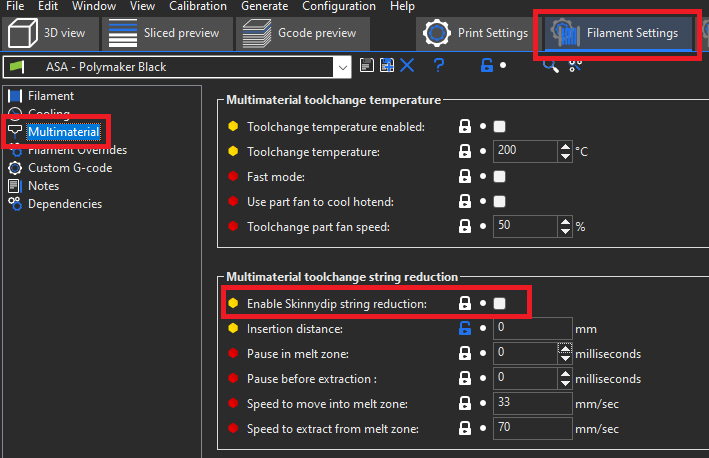
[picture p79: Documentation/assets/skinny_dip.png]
Skinnydip disabling
> <br><br>
> It's probably also a good idea to zero out the distances below.
> Doing this prevents Superslicer from pushing out a blob of filament before cutting the tip.

### Turning off slicer wipetower
To switch to a custom purge system you need only to untoggle the `enable wipetower` option.  All tip forming settings remain the same.

### How to verify configuration
To be sure you have your slicer setup correctly (not doing any tip shaping for example), examine the g-code it creates. Seach for a toolchange section -- this will either have `Tx` commands or will have been parsed to `MMU_CHANGE_TOOL` by the Happy Hare moonraker extension depending on where you are examining the file. Anyway, look at the g-code around the toolchange. It should be clean like this:
```
;--------------------
; CP TOOLCHANGE START
; toolchange #1
; material : ASA -> ASA
;--------------------
; WIPE_TOWER_START
M220 S100
; CP TOOLCHANGE UNLOAD
;WIDTH:0.6
;WIDTH:0.5
M104 S260
; Cooling park
G4 S0
; filament end gcode 
T0
M106 S255
SET_PRESSURE_ADVANCE ADVANCE=0.025 SMOOTH_TIME=0.001 EXTRUDER=extruder
```
And not like this (this is simply one example, many other are more obvious):
```
;--------------------
; CP TOOLCHANGE START
; toolchange #2
; material : ASA -> ASA
;--------------------
; WIPE_TOWER_START
M220 S100
; CP TOOLCHANGE UNLOAD
;WIDTH:0.6
;WIDTH:0.5
; Retract(unload)
G1  X204.504 Y102.283 E-15.0000
G1 E10.4965
G1 E2.9990
G1 E1.4995
; Cooling park
G1 E0.0050 F2000
G4 S0
; filament end gcode 
T2
M106 S255
SET_PRESSURE_ADVANCE ADVANCE=0.025 SMOOTH_TIME=0.001 EXTRUDER=extruder
```
Can you see the unwanted 15mm retraction?  That is the first part of tip creation and you don't want the slicer to do this if you have elected to always let Happy Hare do it.

I wish slicers made it easy to toggle tip forming on/off but unfortunately that is not the case, hence the need to inspect an example generated file to verify it is as expected.

### ERCF Setup Steps:
- [Flashing Your Local MCU](https://github.com/Enraged-Rabbit-Community/ERCF_v2/blob/master/Documentation/Flashing-Local-MCU.md)
- [Installing Happy Hare](https://github.com/Enraged-Rabbit-Community/ERCF_v2/blob/master/Documentation/Installing-Happy-Hare.md)
- [Happy Hare Configuration](https://github.com/Enraged-Rabbit-Community/ERCF_v2/blob/master/Documentation/Happy-Hare-Configuration.md)
- [Hardware Configuration Checks](https://github.com/Enraged-Rabbit-Community/ERCF_v2/blob/master/Documentation/Hardware-configuration-checks.md)
- [Hardware Calibration](https://github.com/Enraged-Rabbit-Community/ERCF_v2/blob/master/Documentation/Hardware-Calibration.md)
- [Toolhead Distances](https://github.com/Enraged-Rabbit-Community/ERCF_v2/blob/master/Documentation/Toolhead-Distances.md)
- [Installing KlipperScreen Happy Hare](https://github.com/Enraged-Rabbit-Community/ERCF_v2/blob/master/Documentation/Installing-KlipperScreen.md)
- Slicer Setup
- [Further Mods to Consider](https://github.com/Enraged-Rabbit-Community/ERCF_v2/blob/master/Documentation/Further-Mods.md)

#### Even more Happy Hare info can be found at:
- [Happy Hare Wiki](https://github.com/moggieuk/Happy-Hare/wiki)

### Additional Happy Hare Information:
- [Tip Forming and Purging](https://github.com/moggieuk/Happy-Hare/wiki/Tip-Forming-and-Purging)
- [Toolchange Movement](https://github.com/moggieuk/Happy-Hare/wiki/Toolchange-Movement)

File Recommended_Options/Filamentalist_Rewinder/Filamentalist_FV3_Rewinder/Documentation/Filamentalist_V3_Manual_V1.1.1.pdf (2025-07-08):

# ERCF

### User Community Help on Discord Here! (https://youtu.be/5Qk3N2sKz40)

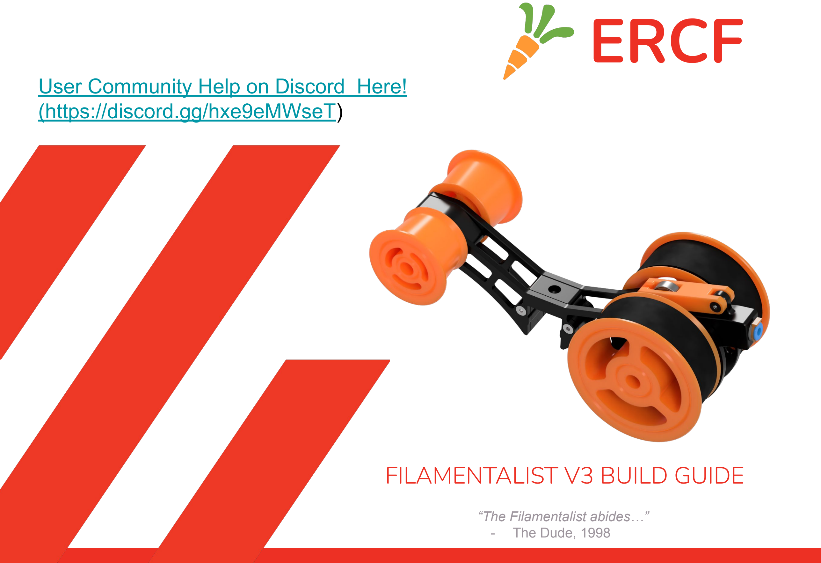
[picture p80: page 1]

# FILAMENTALIST V3 BUILD GUIDE

“The Filamentalist abides…”
- The Dude, 1998

### (https://discord.gg/hxe9eMWseT)

ENRAGED RABBIT CARROT FEEDER (ERCF)

Filamentalist Rewinder V3 CAD version: V1 2 | 2

FILAMENTALIST V3

Introduction
Theory of Operation | 3
Acknowledgements | 4
Configuration/Options | 5
Part Printing Guidelines | 7
STL File Naming Key | 9
Hardware Reference | 10
Required Tools | 11
CAD Files and Parametric Model | 13
Assembly | 16
Tensioner Arm | 17
Tensioner Mount | 18

## TABLE OF CONTENTS

Assembly (cont.)

Center Drive Roller (CDR) | 20
Chassis | 21
CDR/Tensioner Arm | 25
One-Way Bearing Orientation | 26
Rim/Idler Rollers | 27
Tuning | 28
O-Ring Replacement | 29
Questions, Troubleshooting, and Help | 30

Be Kind Rewind
–2008 starring Jack Black and Mos Def

ENRAGED RABBIT CARROT FEEDER (ERCF)

Filamentalist Rewinder V3 CAD version: V1

### INTRODUCTION

The Filamentalist is an integrated solution for buffering and spool holding, providing space savings as well as the potential for filament path reduction, and the associated drag/resistance that comes with long runs from spool to buffer to MMU.
- The Filamentalist uses the axial force delivered by the MMU gear motor along the filament to load and unload from the filament spool.
- An adjustable spring clamp forces the filament against two o-rings that sit on the Center Drive Roller (CDR) to create a high traction interface, for rotating the axle and filament spool.
- A one-way clutch style bearing locks against the Drive Axle and rotates the filament spool, to take up filament during an unload.
- For loading and print extruding, the clutch disengages allowing for effective free-spooling of the filament spool similar to a roller style spool holder.
- The difference in diameter of the filament driven CDR versus the larger Rim Roller that the filament spool sits on provides the needed gear ratio to produce enough rotations to take up, and unload a nearly empty or full filament roll.
- During unloading/buffering, to account for the varying diameter of a spool from full to empty, filament tension will cause the spring loaded arm to lift a small amount and release traction from the o-rings allowing slip to occur between the filament and the o-ring interface of the rewinder (full spool = max slip, empty spool = no/minimal slip). This grip/slip modulation effectively creates a variable gear ratio allowing for clean, tight wraps during unload with a minimum of system drag.

THEORY OF OPERATION

ONE-WAY BEARING

O-RING/FILAMENT
INTERFACE

GEAR RATIO FOR
EMPTY-TO-FULL
SPOOL RANGE

DRIVE AXLE

SPRING TENSION

ENRAGED RABBIT CARROT FEEDER (ERCF)

### INTRODUCTION

I would like to acknowledgement and thank:
thisiscam (on Discord) who shared Muzi Xiaoyang's video of a filament driven rewinder and then continued to partner and share his brilliance in the evolution and optimization of the final product.

The original Beta Test Team (on Discord) who provided design validation and innumerous inputs for design improvements, printability, and simplification of assembly.
Cheesefrog
Grafton
Biokeks
Meltiseugen
JCPhlux
and many more…

All the Early Adopters who allowed a fleet of hundreds of rewinders to help further refine the Filamentalist, the documentation, and volume unit validation. You know who you are!
v6cl (on Discord) for his innovative F1 User Mod that was a core input to the Filamentalist V3 design.
JCPhlux for suggesting the printed clutch design
The ERCF Team for building, supporting, and allowing me to be part of this amazing ecosystem of multi-material printing solutions! Your creativity, commitment, professionalism, collaboration, generosity, and sense of community is an inspiration!

ACKNOWLEDGEMENTS

ENRAGED RABBIT CARROT FEEDER (ERCF)

Filamentalist Rewinder V3 CAD version: V1 5

Things that you need to know include:

There are multiple options for the Filamentalist. Determine which versions/options you want and select the stl's to print accordingly.

- Unit Width: Standard width which supports spool widths from 28mm (i.e. 200gm spools) to 74mm and custom width via the Fusion 360 parametric model
- Drive and Idler Axle bearing size. Step and STL files are provided for the use of either 688 bearings (16mm OD X 8mm ID X 5mm width) or 608 bearings (22mm OD X 8mm ID X 7mm width). Either option can be selected in the provided Fusion 360 parametric model.
- Mounting Style: 2020 center rail mount, 2020 dual rail mount (fits the Filamentalist Enclosure), and Standalone mount

Feed Direction: The orientation of your MMU with respect to your filament spools location or enclosure may require a front, rear, or bottom loading capability from the rewinder. Front and Rear/Bottom feed Tensioner Mount options are provided to support this.

Pre-gate Sensors: If your MMU does not have pre-gate sensors, and the software you use supports them (like Happy Hare), there are CottonTail Lite, Filamentalist Tensioner Mount, and user mod pre-gate sensors that support this. (see the Filamentalist FAQ).

If you are using, or upgrading from an ERCFv1 or v2 version you may want/need a higher torque gear motor. Many in the Beta team ran NEMA 17's spec'd at 55 N-cm max torque and config'd them for 1-1.5A (probably overkill...). A NEMA 17 with 40N-cm or greater holding torque is sufficient. The LDO-42STH47-1684AC stepper is a good option. The ERCF direct drive version is recommended for gaining more speed from a high torque motor. This may not be required, so if you already have built your ERCF, try the Filamentalist with the motor/gearing you have and decide if you need more torque/speed.

INTRODUCTION

CONFIGURATION/OPTIONS CONSIDERATIONS

ENRAGED RABBIT CARROT FEEDER (ERCF)

The standard width Filamentalist has a 50-75mm axle and supports a maximum spool width of 74mm and supports most standard 1, 0.5, and 0.2KG spool sizes and still be able to fit 6 rewinders across the top of a 350 size Voron printer. If you use spools wider than 74mm and you use Autodesk Fusion 360, the provided .f3d file in the CAD directory is a parametric based model allowing you to customize the width of your rewinder to suit your max/min spool widths and/or to design around other available 8mm steel axle lengths (see Parametric CAD Model section in this document). If you are unable to use the parametric model please ask for help on Discord (see cover page and/or page 31 for links).

Because the standard tuning of this design relies on some filament slip at the o-rings, the o-rings may ultimately wear-out. Testing and extrapolation estimates that the wear-out point is greater than 5K cycles. See the O-Ring Replacement section at the end of this document for o-ring swap/replacement instructions.

Enjoy the process of building and utilizing your Filamentalist Rewinder!

INTRODUCTION

CONFIGURATION/OPTIONS CONSIDERATIONS (continued)

ENRAGED RABBIT CARROT FEEDER (ERCF)

The ERCF team has provided the following print guidelines. We recommend you to follow them in order to have the best chance at success with your parts. There are often questions about substituting materials or changing printing standards, but we recommend you follow these.

The majority of mechanical issues users experience with the ERCF and its supporting components can be traced back to print quality and and accuracy. Please take the time to print the calibration tools and dial in your printer before moving forward.

INTRODUCTION

FDM MATERIAL
The Filamentalist was designed for, and
tested with ABS and ASA. Based on the tolerance requirements of the design we recommend to only use ABS OR ASA. Some users have built with other materials such as PLA but you may need to adjust your printer’s calibration for some press-fit and tight tolerance parts.

LAYER HEIGHT
Recommended : 0.2mm
First Layer: 0.25mm

INFILL PERCENTAGE
Recommended: 40%

EXTRUSION WIDTH
Recommended : Forced 0.4mm

WALL COUNT
Recommended : 4

INFILL TYPE
Grid, Gyroid, Honeycomb, Triangle or Cubic.

SOLID TOP/BOTTOM LAYERS
Recommended : 5

### PART PRINTING GUIDELINES

ENRAGED RABBIT CARROT FEEDER (ERCF)

IMPORTANT !! The Filamentalist design relies on multiple press-fits for bearings, axle, and the ECAS04 fitting as well as thread-cut holes. As a result, printer calibration is important. The Print_Calibration_Tool.stl is included. It is highly recommended that you print this block first, check fits, and make adjustments to extrusion multipliers and/or slicer scaling if needed before printing the Filamentalist parts.

INTRODUCTION

### THE PRINT CALIBRATION TOOL

Print_Calibration_Tool.stl

M3 Thread Cutting Hole

ECAS04 Hole
(tight press fit)

TESTS
Insert the different pieces of hardware in their dedicated positions.

The ECAS fitting should be a tight press fit. If the plastic cracks after ECAS insertion or the ECAS is a loose fit then extrusion rates and/or interior hole settings need to be adjusted in your slicer. You may need to cut the print with clippers to remove the ECAS for reuse after checking fit.

You should be able to hand press in a 688/608 bearing into the pocket. It is acceptable if additional force, like light hammer taps is required to fully seat the bearing. The bearing can be removed by inserting an 8mm axle/rod through the bearing and rocking the rod back and forth while gently pulling on the rod, “walking” the bearing out of the pocket.

Screw an M3 screw into the provided 2.7mm diameter hole. The screw should tightly screw in and cut threads into the plastic. If the ECAS and 688/608 bearing press in nicely but this hole is tight, no print adjustments need to be made but M3 screw holes may need to be opened up hand twisting a 2.5mm drill bit.

688/608 Bearing Hole
(easy press fit)

M3 Clearance Hole

8mm Axle Hole
(easy press fit)

ENRAGED RABBIT CARROT FEEDER (ERCF)

FILE NAMING
By this time you should have already downloaded our STL files from the ERCF GitHub. This is how to use the naming conventions.

[a]_Part_Name_{Bearing_Size}_{Quantity_Required}_[option].stl

Example [a]_Rim_Roller_688_Bearing_x2.stl

INTRODUCTION

PRIMARY COLOR
Example
Tensioner_Mount_Std.stl
These files will have nothing at the start of the filename.

ACCENT COLOR
Example
[a]_Tensioner_Arm.stl
These files have an ‘’[a]_’’ prefix to denote that they should be printed with an
accent color.

BEARING SIZE
Filenames with an
‘’688_Bearing’’ or
“608_Bearing” after the file name are specific to the
bearing size option you choose to build.

QUANTITY REQUIRED
Filenames ending with ‘’_x#’’ are telling you the quantity of that part required to build a single rewinder

STL FILE NAMING KEY

[option]
Filenames with an “[option]” after the filename are build options/alternatives such as:
- Mount style
- Pre-gate sensor included in Tensioner Mount
- Printed clutch vs One-Way bearing

ENRAGED RABBIT CARROT FEEDER (ERCF)

INTRODUCTION

FLAT HEAD COUNTERSUNK SCREW (FHCS)
Metric fastener with a cone shaped head and a flat top.

ISO 10642

SOCKET HEAD CAP SCREW (SHCS) Metric fastener with a cylindrical head and hex drive. The most common fastener used on the ERCF.

ISO 4762

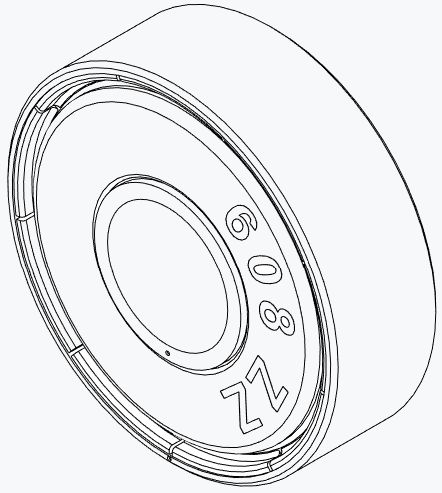
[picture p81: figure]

WASHER
Plain metal stamped washer.

DIN 125

688/608 BEARING
For the Filamentalist, the 2RS (sealed) style is preferred but can be used with the open or ZZ (shielded) style.

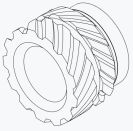
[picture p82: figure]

HEAT SET INSERT
Brass, threaded, with ridges on the outside. Heat to approx 250C with soldering iron and push into a hole in the plastic. Plastic cools and solidifies around the knurls/ridges for excellent resistance to torque and pull-out.

SPRING
For the Filamentalist, 304 Stainless Steel,6mm OD, 0.6mm Wire Size, 15mm Free Length spring used in Tensioner Assembly.

ECAS FITTING
4mm Push -Fit PTFE tubing fitting.

HARDWARE REFERENCE

ENRAGED RABBIT CARROT FEEDER (ERCF)

INTRODUCTION

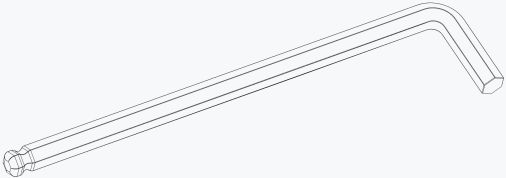
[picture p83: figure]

2.5MM HEX DRIVER
Adjustment of the Tensioner screw in this design benefits from the use of a 2.5mm hex driver. The ball-end style is preferred. This driver is also used for the axle set screws on the Rim Rollers.

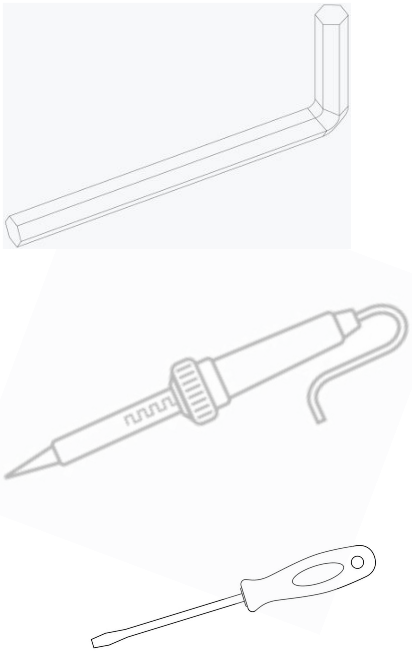
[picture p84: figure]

2MM HEX DRIVER
The 2mm hex driver is used on the M3 FHCS screws in this build.

SOLDERING IRON
For the insertion of the single heat set insert in the Tensioner Mount part.

TOOLS

SMALL FLAT BLADED SCREWDRIVER To aid in the removal of built-in supports.

ENRAGED RABBIT CARROT FEEDER (ERCF)

INTRODUCTION | TOOLS

ANGLE GRINDER/DREMEL
For cutting 8mm axle rods/tubes to length if
required.
VISE
A vise is handy cutting 8mm axles and pressing the one-way bearing into the CDR.
CAD SOFTWARE
Filamentalist_V3_688/608_bearing.step or Filamentalist_V3_(parametric).f3d
Software is a tool too! The CAD file for the Filamentalist was designed to be used along with this manual as a supplement or reference, even if you aren’t a CAD Pro. You can use the free edition of Fusion360, or your choice of CAD program such as TinkerCAD, onshape, or FreeCAD.
SUPERGLUE
Yes, we consider this a tool. Superglue may be useful if your print tolerances result in slip-fits for the bearings and ECAS. Cheap, single-use gel tubes are fine.

PRINT CALIBRATION TOOL
https://github.com/Enraged-Rabbit-Community/ERCF_v2/tree/master/Recommended_Options/Filamentalist_Rewinder/Filamentalist_FV3/Stls/Tools (https://github.com/Enraged-Rabbit-Community/ERCF_v2/tree/master/Recommended_Options/Filamentalist_Rewinder/Filamentalist_FV3/Stls/Tools) It is highly recommended that you print this Print_Calibration_Tool.stl part first, check fits of M3 screws (both slip fit and thread cutting), 608/688 bearings, 8mm axle lightpress/slip fit, and the ECAS04 press fit. Make adjustments to extrusion multipliers and/or slicer scaling if needed before printing the Filamentalist parts.

ENRAGED RABBIT CARROT FEEDER (ERCF)

We have provided the Filamentalist CAD files (https://github.com/Enraged-Rabbit-Community/ERCF_v2/tree/master/Recommended_Options/Filamentalist_Rewinder/Filamentalist_FV3_beta/CAD/Filamentalist_V3_beta_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 and Filamentalist_V3_beta_(parametric)_V##.f3d), so that you can follow along with the instructions in a 3D view, if you like.

The CAD file is organized into folders based on assemblies referenced in this manual. First hide all the parts, and then reveal the parts up to the step you are on in this manual, and the CAD should match what you are building.

All of the non-printed parts are in each assembly’s Hardware folder.

INTRODUCTION

USING THE CAD FILES

ENRAGED RABBIT CARROT FEEDER (ERCF)

If you are using Autodesk Fusion 360 the “Filamentalist_V3_(parametric).f3d file provided in the CAD folder is a parametric based model allowing you to customize the width of your rewinder to suit your max/min spool widths and/or to design around a standard available steel axle length. The model will update and accurately show the results of these parameters to help you visualize the acceptability of the result as well as provide reference dimensions to aid in part sourcing.
To customize your Filamentalist width and axle sizing, load the model, make sure you are in the "Solid" menu, and then select "Modify" and "Change Parameters"

INTRODUCTION

THE PARAMETRIC CAD MODEL

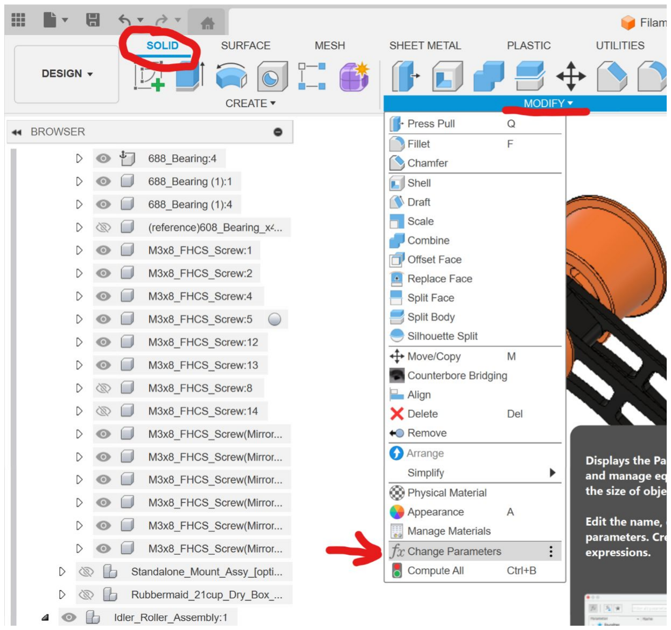
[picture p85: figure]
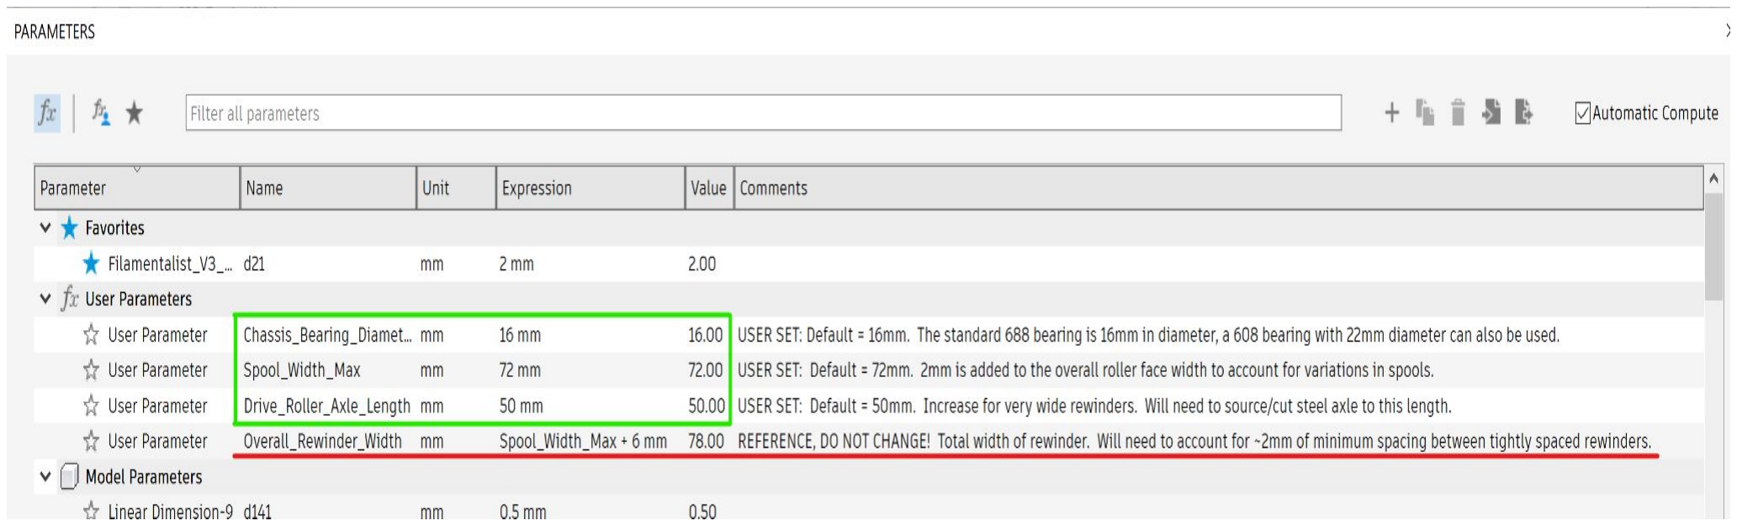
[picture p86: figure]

Adjust the following parameters to meet your needs:
Chassis Bearing Diameter - Set to 16mm if you are using 688 bearings for the Drive and Idler axles or 22mm for 608 bearings. This setting creates unique Chassis_L/R, Rim Roller, and Rear Filamentalist Enclosure Mount parts. Any other setting than 16 or 22mm will result in errors in the model.

(parameter descriptions continued on next page)

ENRAGED RABBIT CARROT FEEDER (ERCF)

INTRODUCTION

THE PARAMETRIC CAD MODEL (continued)

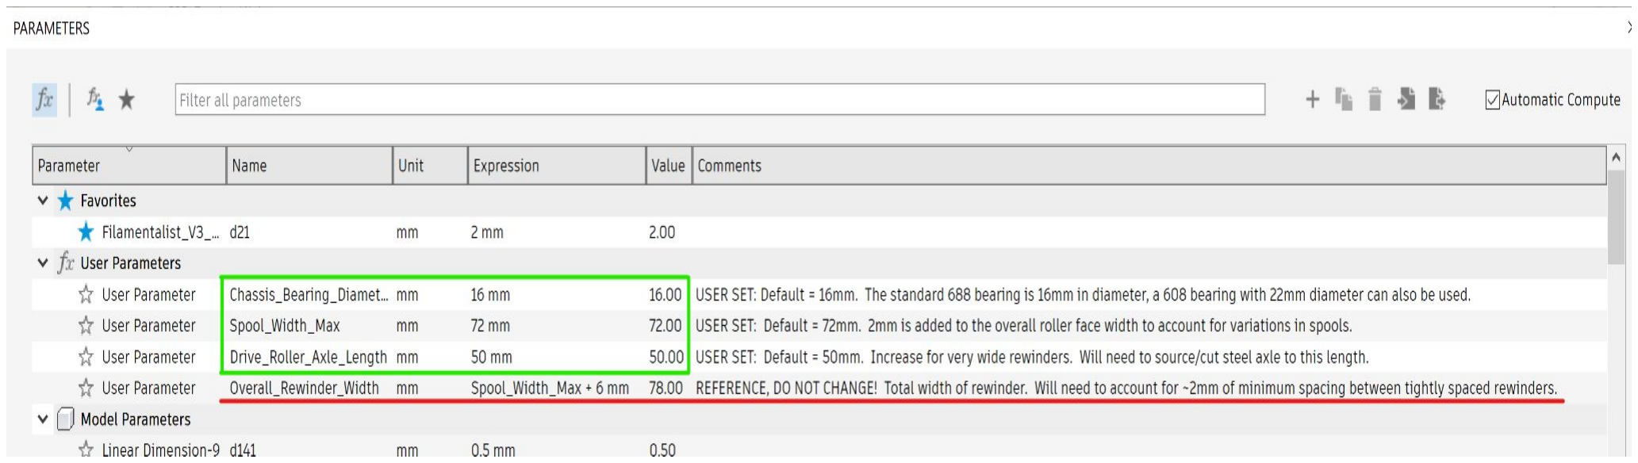
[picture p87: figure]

Adjust the following parameters to meet your needs (continued from previous page):
Spool_Width_Max - The default is 72mm which should accommodate 99% of the 1KG spools on the market. Set this to accommodate the widest filament spool you expect to use. 2mm will be added to this number in the design to allow for spool width and rim straightness/variation.

Drive Roller Axle Length - The default is 50mm. If you already have 80mm axles from the Classic Filamentalist version these can be used with no need to change the parameters in the model. Changing this setting allows you to visualize how a custom (long) axle length will fit, especially if you increase the Spool_Width_Max parameter for a custom wide rewinder.

Overall_Rewinder_Width: REFERENCE PARAMETER. DO NOT CHANGE THIS! This is included as an aid to assess the results of your inputs. You can iterate with changes to the above user inputs to arrive at the desired Overall Rewinder Width for your space, enclosure. Or application.

The model will update to show the results of these parameters to help you visualize the acceptability of the result.

### OVERVIEW

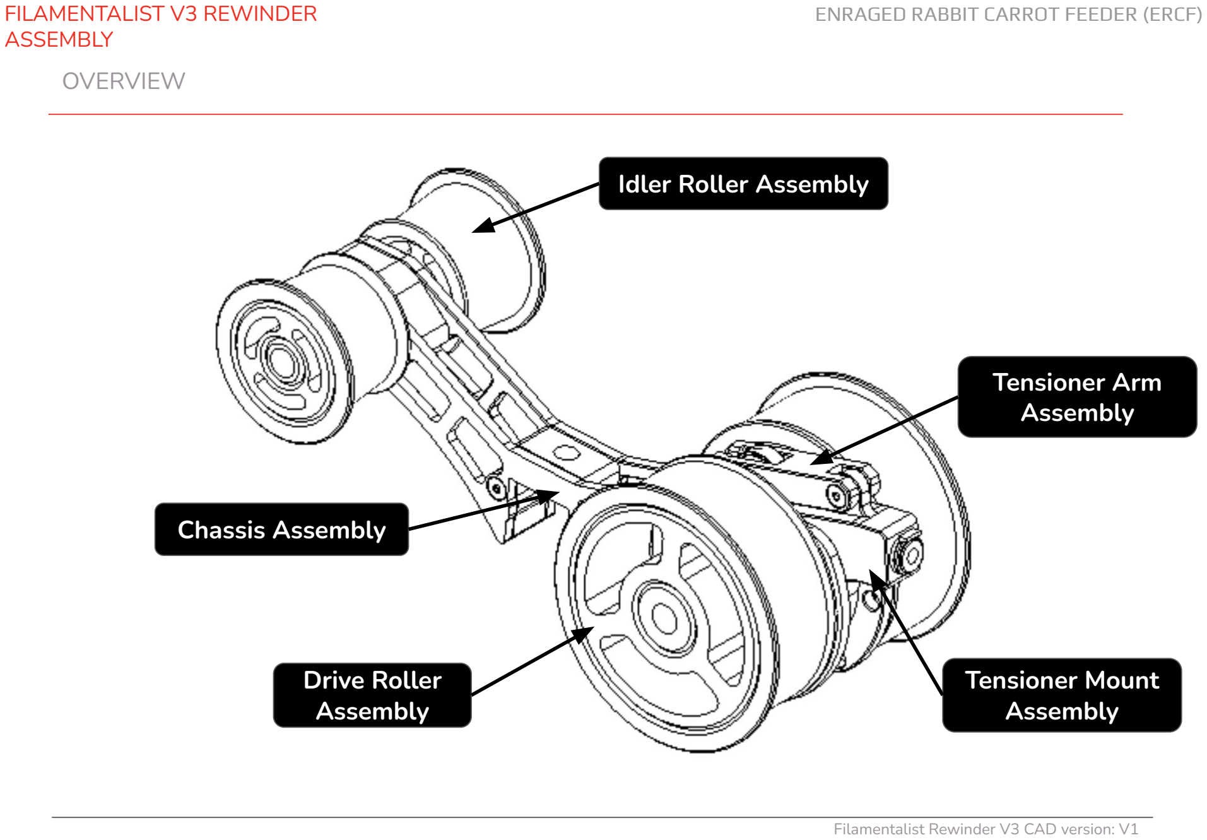
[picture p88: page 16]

ENRAGED RABBIT CARROT FEEDER (ERCF)

FILAMENTALIST V3 REWINDER
ASSEMBLY

## Drive Roller Assembly

## Idler Roller Assembly

## Chassis Assembly

## Tensioner Arm Assembly

## Tensioner Mount Assembly

ENRAGED RABBIT CARROT FEEDER (ERCF)

TENSIONER ARM ASSEMBLY

### EXPLODED VIEW

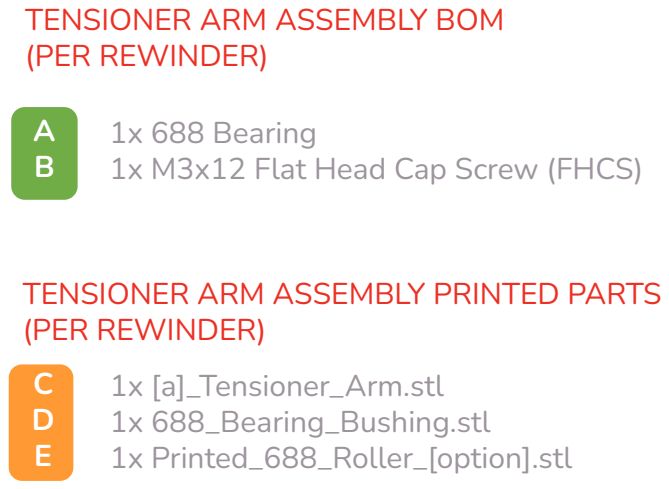
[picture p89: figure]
TENSIONER ARM ASSEMBLY BOM (PER REWINDER); 1x 688 Bearing 1x M3x12 Flat Head Cap Screw (FHCS); 1x [a]_Tensioner_Arm.stl 1x 688_Bearing_Bushing.stl 1x Printed_688_Roller_[option].stl; TENSIONER ARM ASSEMBLY PRINTED PARTS (PER REWINDER)

### ASSEMBLY INSTRUCTIONS

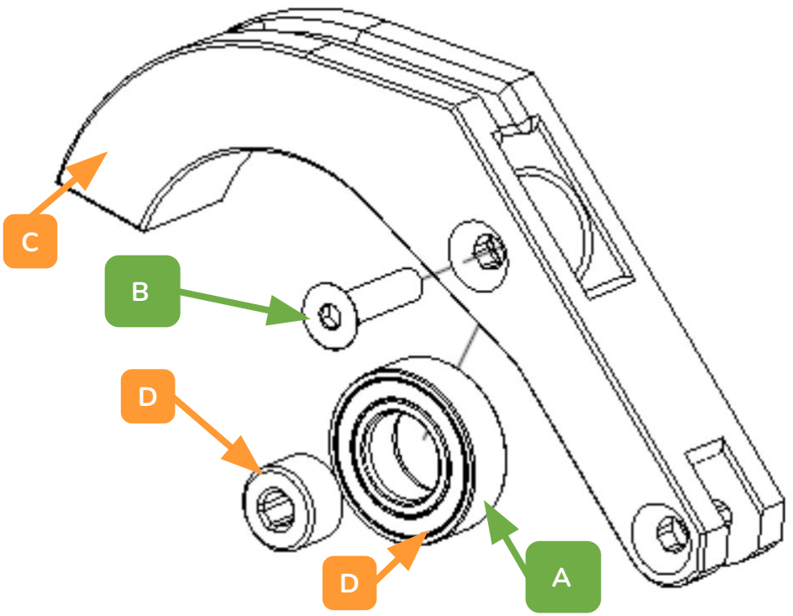
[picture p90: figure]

1. **Note: If you don’t have or want to use a 688 bearing in the Tensioner Arm, the Printed_688_Roller_[option].stl file is provided to use instead.
2. Insert the 688 Bearing Bushing printed part into 688 bearing bore and slide up into Tensioner Arm printed part.
3. Place M3x12 FHCS screw into Tensioner Arm and through the 688 Bearing Bushing and 688 Bearing, cutting threads into plastic of the Tensioner Arm. Only moderate force is required to cut the threads and secure the 688 bearing. Turning the screw with too much force will strip out the plastic threads.

ENRAGED RABBIT CARROT FEEDER (ERCF)

TENSIONER MOUNT
ASSEMBLY
TENSIONER MOUNT ASSEMBLY BOM | EXPLODED VIEW
(PER REWINDER)

1x Heat Set Insert
| 1x ECAS04 1x ECAS04 Locking Clip (stl is available to print)

TENSIONER MOUNT ASSEMBLY PRINTED PARTS

A
B
C

C

D

E

1x ECAS_Clip_[optional_print].stl
(print if not included with ECAS04 purchased part) 1x Tensioner_Mount_Std.stl
or
1xTensioner_Mount_Microswitch_[option].stl
(see next page)
Built-in support that is part of the Tensioner_Mount stl’s but needs to be included if making stl from CAD files)

(PER REWINDER)

D

B

### ASSEMBLY INSTRUCTIONS

1. Remove built-in support (part E) from Tensioner Mount part. A small flat bladed screwdriver placed in the notch works well.
2. Install the heatset insert into the Tensioner Mount part.
3. Insert the ECAS04 into the Tensioner Mount. This should be a tight press fit. One method for installing is to place the ECAS04 on a sturdy surface like a table or counter top and press the Tensioner Mount part downward onto the ECAS04. Ensure the ECAS04 is fully seated against, and aligned to the face of the Tensioner Mount. NOTE: once tubing is installed, secure with an ECAS Locking Clip. If clips were not provided, the ECAS_Clip_[optional_print].stl can be printed.
4. Although not necessary to install now, use of an ECAS04 locking Clip is required once PTFE tubing is installed.
5. If installing a microswitch for filament sensing please refer to the next page.

A

E

C

Tensioner_Mount_Microswitch_[option].stl

Support
removal
notch

C

ENRAGED RABBIT CARROT FEEDER (ERCF)

[OPTIONAL] TENSIONER MOUNT MICROSWITCH ASSEMBLY

### EXPLODED VIEW - LEVER SWITCH

TENSIONER MOUNT MICROSWITCH ASSEMBLY BOM (PER REWINDER)

1x D2F-01FL-D3 Microswitch (lever style)
or
1x D2F-01F-D3 Microswitch (button switch - no lever) 1x MR85 Bearing
or
8x3 Disc Magnet
or
6x3 Disc Magnet
2x M2x8 screws (SHCS or BHCS)

A

B

C

D
E
F

1x Tensioner_Mount_Microswitch_[option].stl
1x 6x3_Magnet_Holder.stl (if using 6x3 magnet)
1x Printed_Switch_Lever.stl (if not using lever switch)

TENSIONER MOUNT MICROSWITCH ASSEMBLY PRINTED PARTS (PER REWINDER)

D

B
MR85 Bearing, or
8x3 Magnet, or
6x3 Magnet in Holder

### ASSEMBLY INSTRUCTIONS

1. Install the MR85 bearing, 8x3 Disc Magnet, or 6x3 Disc Magnet installed in printed 6x3_Magnet_Holder part into the slot in the Tensioner Mount part.
2. If using the button switch (no lever), install the Printed_Switch_Lever printed part into the slot in the Tensioner Mount part. Carefully push back into slots until the barbs click into place.
3. Install the Microswitch into the Tensioner Mount using the M2 screws, cutting threads into the plastic.

A

C

E

### EXPLODED VIEW - BUTTON SWITCH

F

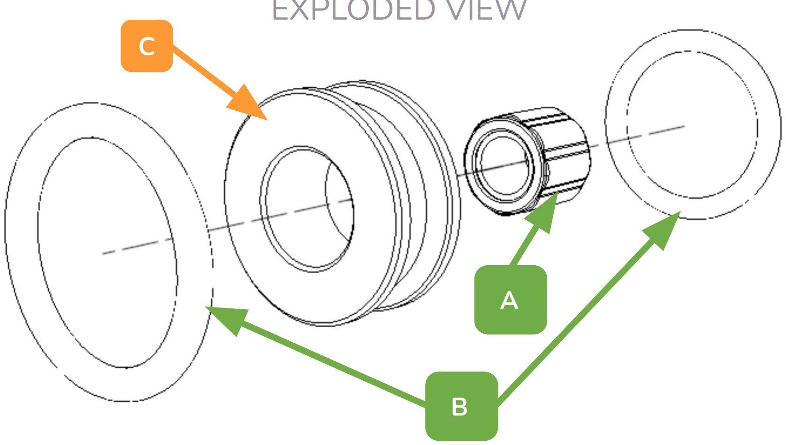
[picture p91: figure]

ENRAGED RABBIT CARROT FEEDER (ERCF)

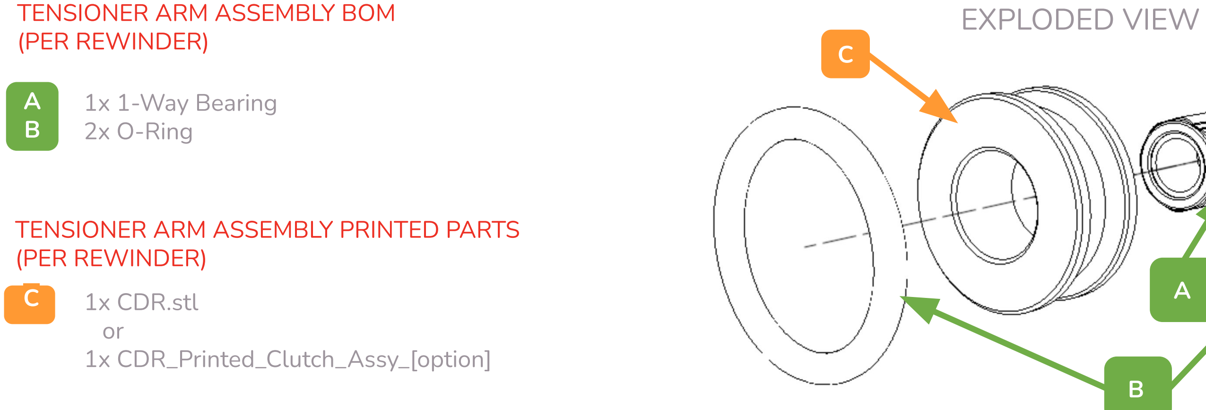
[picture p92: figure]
TENSIONER ARM ASSEMBLY BOM; EXPLODED VIEW; (PER REWINDER); 1x 1-Way Bearing; 2x O-Ring; C 1x CDR.stl or 1x CDR_Printed_Clutch_Assy_[option]; TENSIONER ARM ASSEMBLY PRINTED PARTS (PER REWINDER)

CENTER DRIVE ROLLER (CDR)
ASSEMBLY

### ASSEMBLY INSTRUCTIONS

1. Press the 1-Way Bearing into the CDR part. A bench vise, c-clamp, quick-grip/trigger ratcheting clamp, or soft jaw pliers can be used. Ensure the 1-Way bearing is centered within the CDR.
2. Stretch the (2) o-rings onto the CDR.

### EXPLODED VIEW

CHASSIS ASSEMBLY OVERVIEW; 1x Chassis_L.stl 1x Chassis_R.stl 1x 2020_Mnt_Center_Spacer.stl (or, mount options pg. 23) 1x 2020_Mnt_Spacer_Rear.stl (or, mount options below pg. 23) 1x Idler_Roller_Axle.stl

ENRAGED RABBIT CARROT FEEDER (ERCF)

CHASSIS ASSEMBLY BOM
(PER REWINDER)

4x 688/608 Bearing
12x M3x8mm Flat Head Cap Screw (FHCS)
Tensioner Mount Assembly

CHASSIS ASSEMBLY PRINTED PARTS

FILAMENTALIST ENCLOSURE MOUNT PARTS (PER REWINDER); 1x Fil_Encl_Rear_Mnt_R_[option] 1x Fil_Encl_Rear_Mnt_L_[option] 1x Fil_Encl_Frnt_Mnt_R_[option] 1x Fil_Encl_Frnt_Mnt_L_[option]

CHASSIS MOUNT OVERVIEW
(Rear Load configuration shown)

ENRAGED RABBIT CARROT FEEDER (ERCF)

STANDALONE FRONT/REAR MOUNT

STANDALONE CENTER MOUNT

STANDALONE FRONT/REAR MOUNT BOM
(PER REWINDER)
A 2x M3x8mm Flat Head Cap Screw (FHCS)
STANDALONE FRONT/REAR MOUNT PARTS
1x Standalone_Mnt_Rear_R_[option]
1x Standalone_Mnt_Front_R_[option]
1x Standalone_Mnt_Front_L_[option]

STANDALONE CENTER MOUNT PARTS
F 1x Standalone_Cntr_Mnt_[option].stl

FILAMENTALIST ENCLOSURE MOUNT BOM
2x M3x8mm Flat Head Cap Screw (FHCS)
4x M3x12mm Socket Head Cap Screw
(SHCS)

FILAMENTALIST ENCLOSURE MOUNT

ENRAGED RABBIT CARROT FEEDER (ERCF)

CHASSIS ASSEMBLY - STEP 1

### ASSEMBLY INSTRUCTIONS

1. Hand press (2) 688 or 608 bearings (depending on version printed) into
the bearing pockets of the Chassis_R part.
2. Align the pegs of 2020_Mnt_Rear_Spacer with the peg pockets in Chassis_R and secure with (2) M3x8mm FHCS screws.
2.1. If using Filamentalist Enclosure mounts use Fil_Encl_Rear_Mnt_R_[option] in place of the Spacer part (see next page).
3. Align the pegs of 2020_Mnt_Center_Spacer with peg pockets in Chassis_R part and secure with (2) M3x8mm FHCS screws.
3.1. If not mounting to a 2020 center rail and you want a stiffer chassis, install the 1x Chassis_Cntr_Spacer_[option]. If using the center Standalone mount then install the 1x Standalone_Mnt_R_[option]
3.2. Or, if using the Standalone mount install the Standalone_Cntr_Mnt part.
4. Secure the Tensioner Mount assembly with (2) M3x8mm FHCS screws in either the front or rear load orientation.
CHASSIS ASSEMBLY BOM | EXPLODED VIEW
(PER REWINDER)
2x 688/608 Bearing
6x M3x8mm Flat Head Cap Screw (FHCS)
Tensioner Mount Assembly

E
F

G

1x Chassis_R.stl
1x 2020_Mnt_Center_Spacer.stl
(or, see Chassis Mount options pg. 22) 1x 2020_Mnt_Rear_Spacer.stl
(or, see Chassis Mount options pg. 22)

CHASSIS ASSEMBLY PRINTED PARTS (PER REWINDER)

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
(FRONT LOAD
ORIENTATION)

C
(REAR LOAD
ORIENTATION)

ENRAGED RABBIT CARROT FEEDER (ERCF)

CHASSIS ASSEMBLY - STEP 2

### ASSEMBLY INSTRUCTIONS

1. Hand press (2) 688 or 608 bearings (depending on version printed) into
the bearing pockets of the Chassis_L part.
2. Insert the Idler_Roller_Axle part through the 2020_Mount_Rear_Spacer part and bearing.
3. If using the Filamentalist Enclosure or Front/Rear Standalone Mount options (see pg. 22), screw the two front mounts together with a M3x8 FHCS screw and insert into the peg holes at the front of the Chassis_R part.
4. Secure the Chassis_L part with (6) M3x8mm FHCS screws at the 2020_Mnt_Center_Spacer, 2020_Mnt_Rear_Spacer, and Tensioner Mount Assembly aligning hole locations.

### EXPLODED VIEW

CHASSIS ASSEMBLY BOM
(PER REWINDER)

2x 688/608 Bearing
6x M3x8mm Flat Head Cap Screw (FHCS)

C
D

1x Chassis_L.stl
1x Idler_Roller_Axle.stl

CHASSIS ASSEMBLY PRINTED PARTS (PER REWINDER)

A
B

A

B
C D

ENRAGED RABBIT CARROT FEEDER (ERCF)

CDR/TENSIONER ARM ASSEMBLY

CDR/TENSIONER ARM BOM (PER REWINDER); 1x CDR Assembly 1x Tensioner Arm Assembly 1x 8mm Steel Axle 1x M3x12mm Flat Head Cap Screw (FHCS) 1x M3x30mm Socket Head Cap Screw (SHCS) 1x M3 Washer 1x Spring

### ASSEMBLY INSTRUCTIONS


1. Attach Tensioner Arm Assembly with 1x M3X12mm Flat Head Cap Screw (FHCS)
2. Check for correct CDR/One-Way bearing orientation per pg. 27 and then drop CDR Assembly into Tensioner Mount “pocket”.
3. Insert 8mm axle through chassis bearings and CDR assembly.
4. Verify correct CDR/One-Way bearing orientation per pg. 27 and repeat steps 2 and 3 if necessary.
5. Place an M3 washer followed by the spring onto a M3x30 SHCS screw, insert through slot in Tensioner Arm, and screw into heat set insert in the Tensioner Mount (leave spring untensioned for now).

### EXPLODED VIEWS

ENRAGED RABBIT CARROT FEEDER (ERCF)

ONE-WAY BEARING ORIENTATION


One-Way bearing locks when Rim Roller/Axle is held and Center Drive Roller is rotated in the direction of filament unload/eject (in the pictures above clockwise for front load configuration, counter clockwise for rear/bottom load)

FRONT LOAD CONFIGURATION | REAR/BOTTOM LOAD CONFIGURATION

ENRAGED RABBIT CARROT FEEDER (ERCF)

### RIM/IDLER ROLLER ASSEMBLY

### ASSEMBLY INSTRUCTIONS

1. Stretch Rubber Bands onto Rim Rollers.
2. Ensure axle is centered within the chassis bearings within +/-1mm.
3. Slide Rim Rollers onto steel axle and flush against chassis bearings. Insert M3 screws (length 12mm through 16mm) and tighten with moderate pressure against axle. Ensure Rim Rollers do not compress chassis inward checking that the Tensioner arm can move freely between the chassis parts.
4. Slide Idler Rollers onto Idler Axle. Drive M3x12mm FHCS screws will be driven through the thin support web on the Idler Roller and into the Idler Axle.
RIM/IDLER ROLLER BOM | EXPLODED VIEW
(PER REWINDER)

2x Rubber Band
2x M3x12-16mm Screw (Socket Head preferred)
2x M3x12mm Flat Head Cap Screw (FHCS)

D
E

2x Rim Roller
2x Idler Roller

RIM/IDLER ROLLER PRINTED PARTS (PER REWINDER)

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
ENRAGED RABBIT CARROT FEEDER (ERCF)

### TUNING INSTRUCTIONS

Tune by setting the Tensioner Arm clamping force. The Tensioner Arm does not need an extreme amount of tension.
1. As a bench test (not connected to the MMU yet), insert an ~500mm length of filament into the Tensioner Arm slot, through the o-ring/bearing interface, and out the ECAS side of the Tensioner Mount.
2. Hold one RimRoller and try to pull the filament out in the eject direction.
3. The slip force/resistance should “light-to-moderate” (~0.2-0.3 kg or ~7-10 oz). Adjust the spring tensioner screw accordingly and err on the light side for a starting point.
4. Once a spool is loaded on the rewinder pull ~1m of filament in the load direction. Filament should stay tight on the spool (no loose loops). If loose loops form this indicates that the One-Way Bearing/Center Drive Assembly may be installed backwards (return to CDR/TENSIONER ARM ASSEMBLY step), or the One-Way bearing is too tight on the Center Drive Roller Axle (see Filamentalist Troubleshooting Guide (https://github.com/Enraged-Rabbit-Community/ERCF_v2/blob/master/Recommended_Options/Filamentalist_Rewinder/troubleshoot.md) .).
5. Starting with a tightly packed filament roll, push filament back onto the spool to simulate an MMU unload/eject. If loose filament is forming around the filament spool during unload, tighten the spring tensioning screw. If no loose filament is forming around the filament roll, gradually reduce the spring tension until loose filament starts to accumulate and then increase tension in ~1/2 screw turn increments until you feel you have the lightest tension that results in a tightly packed unload.
6. Initial tuning is complete and the rewinder can now be installed into your system. Steps 4 and 5 above can be followed after rewinder installation if additional tuning is required.

Filament
unload/eject
direction

Filament
load/extrude
direction

Feed filament
through slot in
Tensioner Arm

ENRAGED RABBIT CARROT FEEDER (ERCF)

### O-RING REPLACEMENT

You may never need to replace o-rings. Testing and extrapolation estimates that the wear-out point is greater than 5000 cycles. The impact of o-ring wear-out can be reduced by periodically swapping highly used rewinders with low use rewinders in your line-up. Also, o-rings with grooves worn in them can be swapped with their opposing partners to present the unworn side/face to the filament to extend the life of a set. For o-ring replacement, FOLLOW THE STEPS BELOW:

1. Remove one Rim Roller and slide drive axle out of the rewinder.
2. Unscrew the M3x30mm Tensioner Screw, pivot the Tensioner Arm out of the way, and remove the CDR Assembly.
3. Remove the old o-rings (a dental pic or small flat bladed screwdriver works great).
4. Install a new pair of o-rings or reposition the worn o-rings to present unworn surfaces to the filament interface.
5. Replace the “fresh” CDR Assembly back into the rewinder verifying that the Center Drive Roller Assembly/One-Way Bearing is in the correct orientation (see pg. 27) and reassemble the unit.

ENRAGED RABBIT CARROT FEEDER (ERCF)

Questions, Troubleshooting,
and Help
1. If your rewinder is not functioning properly please reference the Troubleshooting guide on Github here: https://github.com/Enraged-Rabbit-Community/ERCF_v2/blob/master/Recommended_Options/Filamentalist_Rewinder/troubleshoot.md (https://github.com/Enraged-Rabbit-Community/ERCF_v2/blob/master/Recommended_Options/Filamentalist_Rewinder/troubleshoot.md)
a. A video demonstrating the heat rework procedure for tight one-way bearings can be found at 4:20 in the Assembly Video here: https://youtu.be/-1cHOcnosxE
2. Common questions are answered in the FAQ on Github here: https://github.com/Enraged-Rabbit-Community/ERCF_v2/blob/master/Recommended_Options/Filamentalist_Rewinder/Filamentalist_FAQ.md (https://github.com/Enraged-Rabbit-Community/ERCF_v2/blob/master/Recommended_Options/Filamentalist_Rewinder/Filamentalist_FAQ.md)
3. There is an active community supporting and improving the Filamentalist rewinder on Discord here:
https://discord.gg/hxe9eMWseT

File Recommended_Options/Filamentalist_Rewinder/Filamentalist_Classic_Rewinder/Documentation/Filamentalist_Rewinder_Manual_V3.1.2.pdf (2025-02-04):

# ERCF

### Video Assembly Guide Here! (https://youtu.be/5Qk3N2sKz40)


# FILAMENTALIST BUILD GUIDE

“The Filamentalist abides…”
- The Dude, 1998

### (https://youtu.be/-1cHOcnosxE)

### User Community Help on Discord Here! (https://youtu.be/5Qk3N2sKz40) (https://discord.gg/hxe9eMWseT)

ENRAGED RABBIT CARROT FEEDER (ERCF)

Enraged Rabbit Filamentalist Rewinder CAD version: V3

2 | 2

FILAMENTALIST

Introduction
Theory of Operation | 3
Acknowledgements | 4
Configuration/Options | 5
Part Printing Guidelines | 7
STL File Naming Key | 9
Hardware Reference | 10
Required Tools | 11
CAD Files and Parametric Model | 14

## TABLE OF CONTENTS

Assembly | 18
Drive Roller | 19
Idler Roller | 22
Tensioner Mount | 24
Base | 29
Tuning | 35
O-Ring Replacement | 36
Questions, Troubleshooting, and Help | 37

Be Kind Rewind
–2008 starring Jack Black and Mos Def

ENRAGED RABBIT CARROT FEEDER (ERCF)

### INTRODUCTION

The Filamentalist is an integrated solution for buffering and spool holding, providing space savings as well as the potential for filament path reduction, and the associated drag/resistance that comes with long runs from spool to buffer to MMU.
- The Filamentalist uses the axial force delivered by the MMU gear motor along the filament to load and unload to and from the filament spool.
- An adjustable spring clamp forces the filament against two o-rings that sit on the drive pulley to create a high traction interface, for rotating the axle and filament spool.
- A one-way clutch style bearing locks against the drive shaft and rotates the filament spool, to take up filament during an unload.
- For loading and print extruding, the clutch disengages allowing for effective free-spooling of the filament spool similar to a roller style spool holder.
- The difference in diameter of the filament driven clutched roller versus the larger roller that the filament spool sits on provides the needed gear ratio to produce enough rotations to take up, and unload a nearly empty or full filament roll.
- During unloading/buffering, to account for the varying diameter of a spool from full to empty filament tension will cause the spring loaded arm to lift a small amount and release traction from the o-rings allowing slip to occur between the filament and the o-ring interface of the rewinder (full spool = max slip, empty spool = no/minimal slip).

THEORY OF OPERATION

ONE-WAY BEARING

O-RING/FILAMENT
INTERFACE

GEAR RATIO FOR
EMPTY-TO-FULL
SPOOL RANGE

ENRAGED RABBIT CARROT FEEDER (ERCF)

### INTRODUCTION

I would like to acknowledgement and thank:
Thisiscam who shared Muzi Xiaoyang's video of a filament driven rewinder and then continued to partner and share his brilliance in the evolution and optimization of the final product.

The Beta Test Team who provided design validation and innumerous inputs for design improvements, printability, and simplification of assembly.
Cheesefrog
Grafton
Biokeks
Meltiseugen
and many more…

All the Early Adopters who allowed a fleet of hundreds of rewinders to help further refine the Filamentalist, the documentation, and volume unit validation. You know who you are!
The ERCF Team for building, supporting, and allowing me to be part of this amazing ecosystem of multi-material printing solutions! Your creativity, commitment, professionalism, collaboration, generosity, and sense of community is an inspiration!

ACKNOWLEDGEMENTS

ENRAGED RABBIT CARROT FEEDER (ERCF)

Things that you need to know include:

There are multiple options for the Filamentalist. Determine which versions/options you want and select the stl's to print accordingly.

- Unit Width: 80mm, 100mm, and custom width via Fusion 360 parametric model
- Mounting Style: Standard (shelf) mount, 2020 rail clip-in mount, 2020 clip-in mount for Filamentalist Enclosure

Based on your mounting needs, you may or may not need to print and install the Base Plate part. It is really only needed if you don't plan to attach the rewinder to a surface.

Feed Direction: The orientation of your MMU with respect to your filament spools location may require a front, rear, or bottom loading capability from the rewinder. Tensioner Mount options are provided to support this.

Pre-gate Sensors: If your MMU does not have pre-gate sensors, and the software you use supports them (like Happy Hare), there are CottonTail pre-gate sensors and Filamentalist Tensioner Mount options that support this.

If you are using, or upgrading from an ERCFv1 or v2 RC1A version you may want/need a higher torque gear motor. Many in the Beta team ran NEMA 17's spec'd at 55 N-cm max torque and config'd them for 1-1.5A (probably overkill...). Grafton's 40 Tooth NEMA 17 Mod (https://www.printables.com/model/692720-ercf-40-tooth-gear-modifiction) is a good addition for gaining more speed from a high torque motor. This may not be required, so if you already have built your ERCF, try the Filamentalist with the motor/gearing you have and decide if you need more torque/speed.

INTRODUCTION

CONFIGURATION/OPTIONS CONSIDERATIONS

ENRAGED RABBIT CARROT FEEDER (ERCF)

The “standard” Filamentalist has an 80mm axle and supports a maximum spool width of 68mm and supports most standard 1, 0.5, and 0.25KG spool sizes and still be able to fit 6 rewinders across the top of a 350 size Voron printer. Some spools such as NinjaFlex and KVP's are too wide to fit the 80mm design. If you use spools wider than 68mm there is also step and stl files posted for a 100mm axle length version. If you are using Autodesk Fusion 360, the provided .f3d file in the CAD directory is a parametric based model allowing you to customize the width of your rewinder to suit your max/min spool widths and/or to design around a standard available steel axle length (see Parametric CAD Model section in this document).

Because the standard tuning of this design relies on some filament slip at the o-rings, the o-rings may ultimately wear-out. Testing and extrapolation estimates that the wear-out point is ~5K cycles. See the O-Ring Replacement section at the end of this document for o-ring swap/replacement instructions.

Questions or input?

Refer to the:

Filamentalist FAQ (https://github.com/Enraged-Rabbit-Community/ERCF_v2/blob/master/Recommended_Options/Filamentalist_Rewinder/Filamentalist_FAQ.md)

Troubleshooting Guide (https://github.com/Enraged-Rabbit-Community/ERCF_v2/blob/master/Recommended_Options/Filamentalist_Rewinder/troubleshoot.md)

Filamentalist Discord Channel (https://discord.gg/uDcGxukRKd)

Enjoy the process of building as much as utilizing your Enraged Rabbit Carrot Feeder (ERCF) and Filamentalist Rewinder!

INTRODUCTION

CONFIGURATION/OPTIONS CONSIDERATIONS (continued)

ENRAGED RABBIT CARROT FEEDER (ERCF)

The ERCF team has provided the following print guidelines. We recommend you to follow them in order to have the best chance at success with your parts. There are often questions about substituting materials or changing printing standards, but we recommend you follow these.

The majority of mechanical issues users experience with the ERCF and its supporting components can be traced back to print quality and and accuracy. Please take the time to print the calibration tools and dial in your printer before moving forward.

INTRODUCTION

FDM MATERIAL
The Filamentalist was designed for, and
tested with ABS and ASA. Based on the tolerance requirements of the design we recommend to only use ABS OR ASA.

INFILL TYPE
Grid, Gyroid, Honeycomb, Triangle or Cubic.

LAYER HEIGHT
Recommended : 0.2mm
First Layer: 0.25mm

INFILL PERCENTAGE
Recommended: 40%

EXTRUSION WIDTH
Recommended : Forced 0.4mm

WALL COUNT
Recommended : 4

SOLID TOP/BOTTOM LAYERS
Recommended : 5

### PART PRINTING GUIDELINES

ENRAGED RABBIT CARROT FEEDER (ERCF)

IMPORTANT !! The Filamentalist design relies on multiple press-fits for bearings and ECAS fittings. As a result, printer calibration is important. A Test_Block stl is included. It is highly recommended that you print this block first, check fits, and make adjustments to extrusion multipliers and/or slicer scaling if needed before printing the Filamentalist parts.

INTRODUCTION

### THE TEST BLOCK CALIBRATION TOOL

Test_Block.stl

M3 Thread Cutting Hole

ECAS Hole

608 Bearing Hole

TESTS
Insert the different pieces of hardware in their dedicated positions: ECAS fitting, M3 screw thread in, and 608 bearing.

The ECAS fitting should be a tight, snap-in fit. If the plastic cracks after ECAS insertion due to too tight a fit or the ECAS is a loose fit then extrusion rates and/or interior hole settings need to be adjusted in your slicer. You may need to cut the print with clippers to remove the ECAS.

You should be able to hand press in a 608 bearing into the pocket. It is acceptable if additional force, like light hammer taps is required to fully seat the bearing. The bearing can be removed by inserting an 8mm axle/rod through the bearing and rocking the rod back and forth while gently pulling on the rod, “walking” the bearing out of the pocket.

Screw an M3 screw into the back side (opposite ECAS hole). The screw should tightly screw in and cut threads into the plastic. If the ECAS and 608 bearing press in nicely but this hole is tight, no print adjustments need to be made but M3 screw holes may need to be opened up hand turning a 2.5mm drill bit.

ECAS

608 Bearing

ENRAGED RABBIT CARROT FEEDER (ERCF)

FILE NAMING
By this time you should have already downloaded our STL files from the ERCF GitHub. This is how to use the naming conventions.

Part_Name]_[Width_Version]_[Quantity_Required]_[option].stl

Example [a]_Rim_Roller_80mm_x2.stl

INTRODUCTION

PRIMARY COLOR
Example Left_Support.stl
These files will have nothing at the start of the filename.

ACCENT COLOR
Example
[a]_Center_Drive_Roller.stl These files have an ‘’[a]_’’ prefix to denote that they should be printed with an
accent color.

WIDTH VERSION
Filenames with an ‘’80mm’’ or “100mm” after the file
name are specific to the
width option you choose to build.

QUANTITY REQUIRED
Filenames ending with ‘’_x#’’ are telling you the quantity of that part required to build a single rewinder

STL FILE NAMING KEY

[option]
Filenames with an ‘“[option]”after the filename or width are build options/alternatives such as:
- Clip-In style mount
- Supports for the Filamentalist Enclosure
- Pre-gate sensors included in Tensioner Mounts

ENRAGED RABBIT CARROT FEEDER (ERCF)


10 | 10

INTRODUCTION

FLAT HEAD COUNTERSUNK SCREW (FHCS)
Metric fastener with a cone shaped head and a flat top.

ISO 10642

SOCKET HEAD CAP SCREW (SHCS) Metric fastener with a cylindrical head and hex drive. The most common fastener used on the ERCF.

ISO 4762

WASHER
Plain metal stamped washer.

DIN 125

SELF TAPPING SCREW
Fastener with a pronounced thread profile that is screwed directly into plastic. Used with optional pre-gate sensor Filamentalist version.

HEAT SET INSERT
Brass, threaded, with ridges on the outside. Heat to approx 250C with soldering iron and push into a hole in the plastic. Plastic cools and solidifies around the knurls/ridges for excellent resistance to torque and pull-out.

608 BEARING
For the Filamentalist, the 2RS (sealed) style is preferred but can be used with the open or ZZ (shielded) style.

ECAS FITTING
4mm Push -Fit PTFE tubing fitting.

SPRING
For the Filamentalist, 304 Stainless Steel,6mm OD, 0.6-1mm Wire Size, 15mm Free Length spring used in Tensioner Assembly.

HARDWARE REFERENCE

ENRAGED RABBIT CARROT FEEDER (ERCF)


11 | 11

INTRODUCTION

BALL-END HEX DRIVER
Adjustment of the Tensioner screw in this design benefits from the use of a 2.5mm ball-end hex driver.

2MM HEX DRIVER
The 2mm hex driver will see a lot of use in this build. A quality driver is strongly recommended. Refer to the sourcing guide for suggestions.

SOLDERING IRON
For the insertion of the single heat set insert in the Tensioner Mount part of the Filamentalist rewinder

SMALL HAMMER
A small hammer my be useful/required to tap in press-fit bearings.

TOOLS

ENRAGED RABBIT CARROT FEEDER (ERCF)

12 | 12
INTRODUCTION | TOOLS

ANGLE GRINDER/DREMEL
For cutting 8mm axle rods/tubes to length if
required.
VISE
A vise is handy cutting 8mm axles.
CAD SOFTWARE
Filamentalist_80mm/100mm.step or Filamentalist_(parametric).f3d
Software is a tool too! The CAD file for the Filamentalist was designed to be used along with this manual as a supplement or reference, even if you aren’t a CAD Pro. You can use the free edition of Fusion360, or your choice of CAD program such as TinkerCAD, onshape, or FreeCAD.
SUPERGLUE
Yes, we consider this a tool. Superglue may be useful if your print tolerances result in slip-fits for the bearings and ECAS. Cheap, single-use gel tubes are fine.

TEST BLOCK TOOL
ERCFv2/Recommended_Options/Filamentalist_Re winder/Stls/Test_Block.stl
It is highly recommended that you print this Test_Block.stl part first, check fits of M3 screws, 608 bearings, and the ECAS fitting, and make adjustments to extrusion multipliers and/or slicer scaling if needed before printing the Filamentalist parts.
AXLE DEPTH TOOL
ERCFv2/Recommended_Options/Filamentalist_Re winder/Stls/##mm_Axle/Axle_Depth_Tool.stl Helps you set the depth that the Rim Roller parts are attached on the axle to ensure free floating CDR Spacer parts and the correct overall width of the rewinder.

ENRAGED RABBIT CARROT FEEDER (ERCF)

If you need assistance with your build you can head over the Filamentalist Discord group and post your questions in the ercf_questions channel. It is the primary medium to help people with their ERCF build and tuning! You can also check the Github page for the latest releases.

INTRODUCTION

### Discord Link (https://discord.gg/uDcGxukRKd)

GitHub Link (https://github.com/Enraged-Rabbit-Community/ERCF_v2/tree/master/Recommended_Options/Filamentalist_Rewinder)

HOW TO GET HELP

ENRAGED RABBIT CARROT FEEDER (ERCF)

We have provided the Filamentalist CAD files (ERCFv2/Recommended_Options/Filamentalist_Rewinder/CAD/Filamentalist_##mm.step and Filamentalist_(parametric).f3d), so that you can follow along with the instructions in a 3D view, if you like.

The CAD file is organized into folders based on the instructions in this manual. First hide all the parts, and then reveal the parts up to the step you are on in this manual, and the CAD should match what you are building.

All of the non-printed parts are in each section’s Hardware folder.

INTRODUCTION

USING THE CAD FILES

ENRAGED RABBIT CARROT FEEDER (ERCF)

If you are using Autodesk Fusion 360 the “Filamentalist_(parametric).f3d file provided in the CAD folder is a parametric based model allowing you to customize the width of your rewinder to suit your max/min spool widths and/or to design around a standard available steel axle length. The model will update and accurately show the results of these parameters to help you visualize the acceptability of the result as well as provide reference dimensions to aid in part sourcing.
To customize your Filamentalist width and axle sizing, load the model, make sure you are in the "Solid" menu, and then select "Modify" and "Change Parameters"

INTRODUCTION

THE PARAMETRIC CAD MODEL


Adjust the following parameters to meet your needs:
Spool_Width_Max - Set this to accommodate the widest filament spool you expect to use. It is recommended to add ~2mm to this number to allow for spool width and rim straightness/variation.

(parameter descriptions continued on next page)

ENRAGED RABBIT CARROT FEEDER (ERCF)


16 | 16

INTRODUCTION

THE PARAMETRIC CAD MODEL (continued)

Adjust the following parameters to meet your needs (continued from previous page):
Spool_Width_Min - Set this to accommodate the narrowest filament spool you expect to use. Due to the width of the Tensioner Assembly the minimum spool width is constrained at 34mm and will default to this number if you enter something less than 34mm. If you don't expect to use narrow spools (like 250kg or 500kg spools) you can set this to a larger number to produce narrower Rim Rollers. Narrower Rim Rollers will reduce print time and filament consumed and may allow for usage of more standard, less expensive, and/or fewer rubber bands but will limit overall future flexibility of your rewinder.

Min_Spool_Rim_Thickness - Normally this can be left at the default of 3mm but if you are trying to squeeze narrow spools onto the rewinder, you are close to that 34mm minimum width, and your narrow spool rims are less than 3mm thick, you can adjust for your thickest rim of your narrowest spool to make it fit the rewinder.

ENRAGED RABBIT CARROT FEEDER (ERCF)


17 | 17

INTRODUCTION

THE PARAMETRIC CAD MODEL (continued)

Adjust the following parameters to meet your needs (continued from previous page):
Axle_Under_Over_Hang - This can be either a positive or negative number and is used to tweak the design to use a standard available axle length (like 80mm or 100mm). A negative number will result in the axle ends sitting inside the footprint of the rewinder but the model logic will not let you underhang more than 5.5mm inside the 608 bearing race to ensure good support of the axles from the bearings. A positive number will result in the axle protruding beyond the footprint of the rewinder. You may want to do this if you are going to use a readily available 100mm length axle but don't need a rewinder that can support spool widths as wide as 86mm, thus saving printing time and plastic by using a lesser Spool_Width_Max like 75mm. The best case scenario is to set this value at 0 and you have the ability to cut shaft stock to the exact length for your desired Spool_Width_Max (i.e. Spool_Width_Max = 75mm to accommodate virtually all 1KG spools and cut shaft to 88.5mm length).

Reference Parameters. DO NOT CHANGE THESE! These are included to assess the results of your inputs. You can iterate with changes to the User inputs to arrive at desired max spool width, standard axle widths, and/or readily available rubber band sizes.

The model will update to show the results of these parameters to help you visualize the acceptability of the result.

### OVERVIEW

## Idler Roller Assembly


ENRAGED RABBIT CARROT FEEDER (ERCF)

FILAMENTALIST REWINDER
ASSEMBLY

## Drive Roller Assembly

## Tensioner Assembly

## Base Assembly

## Tensioner Arm Assembly Tensioner Mount Assembly

ENRAGED RABBIT CARROT FEEDER (ERCF)

### DRIVE ROLLER ASSEMBLY


“You can’t have everything….where would you put it?” –Steven Wright

ENRAGED RABBIT CARROT FEEDER (ERCF)

### DRIVE ROLLER ASSEMBLY EXPLODED VIEW

DRIVE ROLLER ASSEMBLY BOM
(PER CHANNEL)

1x 8x80/100mm Stainless Steel Axle 2x AS568 Standard size 211 O-Ring 1x HF081412 One-Way Bearing 2-6x M3x8 Stainless SHCS Screw 2x Rubber Bands

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
2x [a]_Rim_Roller_80/100mm.stl 1x [a]_Center_Drive_Roller.stl
2x CDR_Spacer.stl
Axle_Depth_Tool.stl

DRIVE ROLLER ASSEMBLY PRINTED PARTS (PER CHANNEL)

A

B

C

F

H

G

D

### ASSEMBLY INSTRUCTIONS

1. Check the resistance of the one-way bearing on the axle. If the resistance is greater than the combined rolling resistance of the rest of the rewinder the one-way bearing will not disengage and freespool properly during filament loads resulting in loose coils on the spool. If you experience this issue please refer to the Filamentalist Troubleshooting Guide. (https://github.com/SkiBikePrint/Filamentalist/blob/main/troubleshoot.md)
2. Stretch O-Rings (part B) onto part G.
3. Press/tap part C into part G. This should be a tight fit. If too loose, use Super Glue or reprint with an increased extrusion factor. If too tight scrape the interior hole of Center Driver Roller with an Xacto knife. Orientation of the one-way bearing does not matter at this point.
4. Install screws into Rim Rollers to cut the threads (using a ball end hex driver makes this easier). Back the screws out a little to allow the axle to be inserted. If center bore of rollers is a close fit, only one screw per roller is required. If a loose fit, use 3 screws per roller to ensure roller is centered on Axle.

I

E

### DRIVE ROLLER ASSEMBLY (continued) EXPLODED VIEW


ENRAGED RABBIT CARROT FEEDER (ERCF)

DRIVE ROLLER ASSEMBLY BOM
(PER CHANNEL)

1x 8x80/100mm Stainless Steel Axle 2x AS568 Standard size 211 O-Ring 1x HF081412 One-Way Bearing 2-6x M3x8 Stainless SHCS Screw 2x Rubber Bands

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
2x [a]_Rim_Roller_80/100mm.stl 1x [a]_Center_Drive_Roller.stl
2x CDR_Spacer.stl
Axle_Depth_Tool.stl

DRIVE ROLLER ASSEMBLY PRINTED PARTS (PER CHANNEL)

### ASSEMBLY INSTRUCTIONS

4. Use Axle Depth Tool to set the correct distance of one Rim Roller from Axle end and tighten screw(s) firmly against Axle. (CAUTION: don’t overtighten/strip threads).
5. Slide Center Drive Roller/One-Way Bearing and CDR Spacers onto Axle (CDR spacers should be a loose fit on axle) and install the second Rim Roller per step 4.
5.1. It is very important that the the CDR spacers and Center Drive Roller spin freely on Axle with~0.5mm space between adjacent parts.
6. Install Rubber Bands onto Rim Rollers.

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
ENRAGED RABBIT CARROT FEEDER (ERCF)

### IDLER ROLLER ASSEMBLY


Q: What do you call a group of rabbits hopping backwards? A: A receding hare line

ENRAGED RABBIT CARROT FEEDER (ERCF)

### IDLER ROLLER ASSEMBLY

### EXPLODED VIEW

DRIVE ROLLER ASSEMBLY BOM (PER CHANNEL); A 2x MR608 Bearing; 1x [a]_Idler_Roller_Female_80mm/100mm.stl 1x [a]_Idler_Roller_Male_80mm/100mm.stl 1x Idler_Roller_Axle_80mm/100mm.stl 1x Axle_Depth_Tool.stl; DRIVE ROLLER ASSEMBLY PRINTED PARTS (PER CHANNEL); ASSEMBLY INSTRUCTIONS; bearing pockets.

1. Press MR608 bearings into parts D and E. These should be a tight fit but insertable by hand. Use the Axle Depth Tool as a pressing aid to ensure bearings are seated fully into
2. Screw parts D and E together until firmly seated against each other.

### TENSIONER MOUNT ASSEMBLY


ENRAGED RABBIT CARROT FEEDER (ERCF)

### BASELINE VERSION

### PRE-GATE SENSOR OPTION VERSION

### REAR LOAD PRE-GATE SENSOR OPTION VERSION

### REAR LOAD OPTION VERSION

Be Kind Rewind
- Jack Black and Mos Def 2008

ENRAGED RABBIT CARROT FEEDER (ERCF)

### TENSIONER MOUNT ASSEMBLY

TENSIONER MOUNT ASSEMBLY BOM (PER CHANNEL)
ECAS Fitting (remove rubber seal)
3mm Heatset Insert

A
B

F
G

1x [a]_Tensioner_Mount_80mm/100mm.stl
1x [a]_ECAS_Clip.stl (if not on-hand)

TENSIONER MOUNT ASSEMBLY PRINTED PARTS
(PER CHANNEL) | A

F

G

ALTERNATE/OPTIONAL PRINTED PART VERSIONS
(PER CHANNEL)
F 1x [a]_Tensioner_Mount_with_Sensor_80mm/100mm.stl
(split to parts in slicer for print-in-place breakaway connector retaining key) 1x [a]_Tensioner_Mount_Rear_Load_80mm/100mm.stl
1x [a]_Tensioner_Mount_Rear_Load_with_Sensor_80mm/100mm.stl

### EXPLODED VIEW

### ASSEMBLY INSTRUCTIONS

B

1. Install 3mm Heatset Insert.
2. Remove rubber seal and press ECAS Fitting into Tensioner Mount, ensuring it sits flush to face of hole. Using the 8mm axle as a pressing tool can help to get fitting fully inserted. Varying
ECAS and print tolerances could result in the ECAS hole cracking. If this happens, use superglue around the ECAS hole and crack(s).

Built-in
removable
support

PRE-GATE SENSOR
OPTION VERSION

REAR LOAD
OPTION VERSION

REAR LOAD
PRE-GATE SENSOR
OPTION VERSION

ENRAGED RABBIT CARROT FEEDER (ERCF)

### TENSIONER MOUNT ASSEMBLY (SENSOR OPTION)

SENSOR OPTION ADDITIONAL BOM ITEMS (PER CHANNEL)

1x D2F-L3 Microswitch
1x JST-XH 2-pin Socket
2x 60mm 24 AWG wire
2x M2x10 Self-tapping screw

A
B
C
D

F 1x [a]_Tensioner_Mount_with_Sensor_80mm/100mm.stl

TENSIONER MOUNT ASSEMBLY PRINTED PARTS
(PER CHANNEL)

A

B

B

F

ALTERNATE/OPTIONAL PRINTED PART VERSIONS
(PER CHANNEL)
F 1x [a]_Tensioner_Mount_Rear_Load_with_Sensor_80mm/100mm.stl

Built-in removable
support

### EXPLODED VIEW

### ASSEMBLY INSTRUCTIONS

1. Break away print-in-place JST-XH socket retaining clip using small flat blade screwdriver.
2. Install microswitch with 2x M2x10mm self tapping screws.
3. Strip 3mm from 24 AWG wire for JST-XH socket and tin with solder.
4. Feed wire through hole in wire slot and out opening for JST-XH socket.
5. Solder 2x wires at 90 degrees to terminals of JST-XH 2-pin socket and press socket into hole. Slide socket retaining clip back into place.
6. Press wire into slot and wrap around to the two switch terminals denoted with red dots in picture to assess length. Cut wire to length leaving 3mm for stripped ends to solder to terminals.
7. Solder wire to switch terminals.
8. Usa a 2-pin JST-XH plug for a harness running to main or MMU board.

BREAK
AWAY

C

D

ENRAGED RABBIT CARROT FEEDER (ERCF)

### TENSIONER ARM ASSEMBLY

TENSIONER ARM ASSEMBLY BOM (PER CHANNEL)

1x MR608 bearing
3x M3x16/18mm FHCS Screw
1x Spring
1x M3 Washer
1x M3x35mm +/- 10mm SHCS Screw

A
B
C
D
E

C
D

1x Tensioner_Arm_Left.stl
1x Tensioner_Arm_Rightstl

TENSIONER ARM ASSEMBLY PRINTED PARTS (PER CHANNEL)

A

B

C

D

Arm orientation for rear load version

| 1. Remove support from part D.

### EXPLODED VIEW

### ASSEMBLY INSTRUCTIONS

2. Lay part D on a flat surface. Slide the 608 bearing onto the bearing post.
Place part C into the 608 bearing and rotate against the part D making sure the
alignment tab seats correctly into the pocket at the bottom of part C.
3. Place a M3x12/16/18 FHCS screw through the bearing mount hole of part C and moderately tighten the screw into part D. Once installed verify that the bearing turns freely.
4. Place a M3x12/16/18 FHCS screw through the hole in part C at the "nose" end and moderately tighten the screw into part D.
5. Install the Tensioner Arm onto the Tensioner Mnt using a 3x16/18mm FHCS screw. Tighten until snug and then back off until the arm rotates freely on the mount.
6. Place an M3 washer followed by the spring onto an M3x25/35/45mm SHCS screw and slide through the slotted hole in the bottom of the Tensioner Arm Assembly. Screw the SHCS screw into the heatset insert of the Tensioner Mnt. No tension should be on the spring at this point.

Remove
Support
C

D

E

ENRAGED RABBIT CARROT FEEDER (ERCF)

### TENSIONER ARM ASSEMBLY

ALTERNATE TENSIONER SCREW ORIENTATION

### ASSEMBLY INSTRUCTIONS


1. Insert the 3mm SHCS Tensioner screw from the bowden side of the rewinder through the heatset insert in the Tensioner Mount and the Tensioner Arm.
2. Insert the spring onto the Tensioner Screw.
3. Place an M3 washer followed by a lock nut, a nut with with threadlocker, or a heatset with threadlocker onto the Tensioner Screw to capture the spring.

If the orientation of your Filamentalist makes it difficult to access the tension adjustment screw you can reverse the 3mm SHCS Tensioner screw.

ENRAGED RABBIT CARROT FEEDER (ERCF)

### BASE ASSEMBLY

“Get back Jojo”
–The Beatles


ENRAGED RABBIT CARROT FEEDER (ERCF)

### BASE ASSEMBLY

### EXPLODED VIEW

DRIVE ROLLER ASSEMBLY BOM (PER CHANNEL); 2x MR608 Bearing; 1x Right_Support.stl 1x Left_Support.stl 1x Base_Plate_80mm/100mm_[option].stl; DRIVE ROLLER ASSEMBLY PRINTED PARTS (PER CHANNEL)

6(10)x M3X8/10/12 Flat Head Cap Screw (FHCS)

ENRAGED RABBIT CARROT FEEDER (ERCF)

### BASE ASSEMBLY

### EXPLODED VIEW

DRIVE ROLLER ASSEMBLY BOM (PER CHANNEL); 2x MR608 Bearing; 1x Right_Support.stl 1x Left_Support.stl 1x Idler Roller Assembly; DRIVE ROLLER ASSEMBLY PRINTED PARTS (PER CHANNEL); ASSEMBLY INSTRUCTIONS; Supports until fully seated.

1. Press MR608 bearings into parts D and E. These should be a tight fit but insertable by hand. If necessary, use the Axle Depth Tool and lightly tap with hammer to ensure bearings are seated fully into bearing pockets.
2. Align the D-shape end of the Idler Roller Assembly Axle and tap/press into one of the

ENRAGED RABBIT CARROT FEEDER (ERCF)

### BASE ASSEMBLY (continued)

ONE-WAY BEARING ORIENTATION One-Way bearing locks when Rim Roller/Axle is held and Center Drive Roller is rotated in the direction of filament unload/eject (clockwise for standard load, counter clockwise for rear load option); Filament unload/eject direction Hold; Turn Clockwise

### ASSEMBLY INSTRUCTIONS (continued)

3. Insert Drive Roller Assembly axle into the MR608 bearing of the Support that has the Idler Roller Assembly installed on it.
3.1. IMPORTANT! Orient the Drive Roller Assembly so that the one-way bearing of the Center Drive Roller locks when rotated in the direction of a filament unload (if using the Tensioner Mount Rear Load option then the one-way bearing must be reversed and operate/lock in the counterclockwise direction with respect to the picture above).
4. Place Tensioner Assembly onto/over Drive Roller Assembly and Idler Roller onto Idler Roller Axle.

### BASE ASSEMBLY (continued)

DRIVE ROLLER ASSEMBLY BOM; EXPLODED VIEW; 1x Right_Support.stl 1x Left_Support.stl 1x Base_Plate_80mm/100mm_[option].stl 1x Idler Roller Assembly; DRIVE ROLLER ASSEMBLY PRINTED PARTS (PER CHANNEL)

ENRAGED RABBIT CARROT FEEDER (ERCF)

(PER CHANNEL)
6(10)x M3X8/10/12 Flat Head Cap Screw (FHCS)
2x MR608 Bearing

ASSEMBLY INSTRUCTIONS (continued)
5. Install other Support onto Center Drive Roller Axle and Idler Roller Axle. Support
may need to be tapped/pressed onto the Idler Roller Axle to be fully seated.
6. Install (6) M3x8/10/12 FHCS screws through Supports and into Tensioner Mount
and Idler Roller Axle.
7. If using the optional Base Plate, install (4) M3x8/10/12 FHCS screws through Base
Plate and into Supports and Tensioner Mount.

ENRAGED RABBIT CARROT FEEDER (ERCF)

### BASE ASSEMBLY (continued)

Filament unload/eject direction Hold; Filament load/extrude direction

8. Verify again that One-Way bearing is installed correctly. Insert a piece of filament through the filament path and tighten the Tensioner Screw to create medium spring tension.
9. Hold the center roller by placing your thumb/finger against the o-rings and try to pull the filament out in the eject direction.
10. The slip force/resistance against the filament should “light-to-moderate” (~0.2-0.3 kg or ~7-10 oz). Adjust the spring tensioner screw accordingly and err on the light side for a starting point.
11. While holding a Rim Roller with one hand, move the filament in the eject direction (see picture above). The Rim Roller should try to rotate against the pressure of your hand.
12. Continuing to hold a Rim Roller, move the filament in the load/extrude direction. The Rim Roller should not try to move and the Center Drive Roller should turn freely.

### ASSEMBLY INSTRUCTIONS (continued)

ENRAGED RABBIT CARROT FEEDER (ERCF)

### TUNING

### TUNING INSTRUCTIONS

Tune by setting the Tensioner Arm clamping force. The arm does not need an extreme amount of tension.
1. As a bench test (not connected to the MMU yet), load a spool of filament onto the rewinder and insert the filament through the o-ring/bearing interface and out the ECAS side of the Tensioner Mount.
1.1. IMPORTANT! The filament should feed through the slot in the “nose” of the Tensioner Arm.
2. Hold the center roller by placing your thumb/finger against the o-rings and try to pull the filament out in the eject direction.
3. The slip force/resistance should “light-to-moderate” (~0.2-0.3 kg or ~7-10 oz). Adjust the spring tensioner screw accordingly and err on the light side for a starting point.
4. Pull ~1m of filament in the load direction. Filament should stay tight on the spool (no loose loops). If loose loops form this indicates that the One-Way Bearing/Center Drive Assembly may be installed backwards (return to Center Drive Roller Assembly step), or the One-Way bearing is too tight on the Center Drive Roller Axle (see Filamentalist Troubleshooting Guide.). (https://github.com/SkiBikePrint/Filamentalist/blob/main/troubleshoot.md)
5. Starting with a tightly packed filament roll, push filament back onto the spool to simulate an MMU unload/eject. If loose filament is forming around the filament spool during unload, tighten the spring tensioning screw. If no loose filament is forming around the filament roll, gradually reduce the spring tension until loose filament starts to accumulate and then increase tension in ~1/2 screw turn increments until you feel you have the lightest tension that results in a tightly packed unload.
6. Initial tuning is complete and the rewinder can now be installed into your system. The same steps above can be followed after rewinder installation if additional tuning is required.

Filament unload/eject direction; Filament load/extrude direction; Feed filament through slot in Tensioner Arm

ENRAGED RABBIT CARROT FEEDER (ERCF)

### O-RING REPLACEMENT

You may never need to replace o-rings. Testing and extrapolation estimates that the wear-out point is ~5K cycles. The impact of o-ring wear-out can be reduced by periodically swapping highly used rewinders with low use rewinders in your line-up. Also, o-rings with grooves worn in them can be swapped with their opposing partners to present the unworn side/face to the filament to extend the life of a set. For o-ring replacement, FOLLOW THE STEPS BELOW:

1. Unscrew the (6) screws of the Right and Left Supports and remove them.
2. Remove the Drive Roller Assembly from under the Tension Mount Arms.
3. Unscrew the set screw(s) on one Rim Roller and remove it from the axle.
4. Slide the CDR Spacer and Center Drive Roller from the axle
5. Remove the old o-rings (a dental pic or small flat bladed screwdriver works great).
6. Install a pair of new o-rings.
7. Reinstall the Center Drive Roller and CDR Spacer back on the axle.
8. Install the Rim Roller back onto the axle.
a. Use Axle Depth Tool to set the correct distance of Rim Rollers from Axle end and tighten screw(s) firmly against Axle.
b. Confirm that the CDR spacers still freely spin on Axle with~0.5mm space between adjacent parts.
9. Verify that the Center Drive Roller Assembly/One-Way Bearing is in the correct orientation and reassembly the unit.

ENRAGED RABBIT CARROT FEEDER (ERCF)

### Questions, Troubleshooting, and Help

1. If your rewinder is not functioning properly please reference the Troubleshooting guide on Github here: https://github.com/Enraged-Rabbit-Community/ERCF_v2/blob/b06b4bec456481a31ca77793b5a11747fa6342c3/Recommended_Options/Filamentalist_Rewinder/troubleshoot.md (https://github.com/Enraged-Rabbit-Community/ERCF_v2/blob/b06b4bec456481a31ca77793b5a11747fa6342c3/Recommended_Options/Filamentalist_Rewinder/troubleshoot.md)
a. A video demonstrating the heat rework procedure for tight one-way bearings can be found at 4:20 in the Assembly Video here: https://youtu.be/-1cHOcnosxE
2. Common questions are answered in the FAQ on Github here: https://github.com/Enraged-Rabbit-Community/ERCF_v2/blob/b06b4bec456481a31ca77793b5a11747fa6342c3/Recommended_Options/Filamentalist_Rewinder/Filamentalist_FAQ.md
3. There is an active community supporting and improving the Filamentalist rewinder on Discord here:
https://discord.gg/hxe9eMWseT

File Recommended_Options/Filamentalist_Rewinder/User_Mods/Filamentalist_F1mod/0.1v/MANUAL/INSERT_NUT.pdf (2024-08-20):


M3 INSERT NUT X 3


M3 INSERT NUT X 3

623 BEARING X 2


M3 INSERT NUT X 4

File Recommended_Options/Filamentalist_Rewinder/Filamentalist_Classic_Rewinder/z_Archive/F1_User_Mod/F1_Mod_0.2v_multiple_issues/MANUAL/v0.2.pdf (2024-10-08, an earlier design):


M3 nut

M3 bolt 6mm


M3 insert nut

M3 insert nut


623 Bearing

M3 bolt 18mm


6x3 magnets


6x3 magnets


M3 bolt 18mm


608 bearing


clutch bearing

O ring x 2


8mm shaft

M3 bolt 8mm

M3 bolt 8mm

M3 bolt 8mm

M3 bolt 8mm


M3 bolt 8mm

M3 bolt 8mm

M3 bolt 8mm


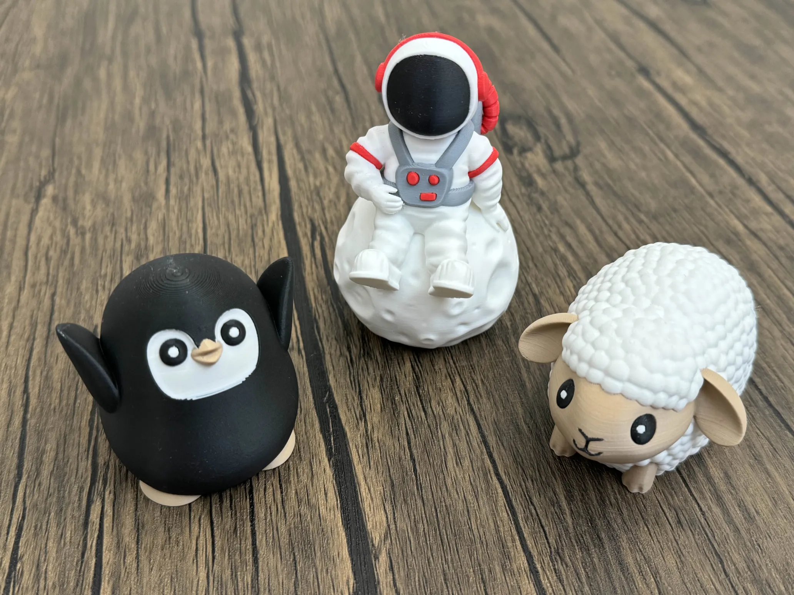
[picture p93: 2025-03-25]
Documentation/assets/example_mmu_print.png

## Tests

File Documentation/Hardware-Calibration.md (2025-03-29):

## Page Sections:
- [Calibration Steps](#---calibration-steps)
  - [1. Servo](#---step-1-calibrate-your-servo)
  - [2. Selector Offsets](#---step-2-calibrate-selector-offsets)
  - [3. Springy Tension](#---step-3-springy-calibration)
  - [4. Gear Stepper](#---step-4-calibrate-your-gear-stepper)
  - [5. Encoder](#---step-5-calibrate-your-encoder)
  - [6. Bowden Length](#---step-6-calibrate-bowden-length)
  - [7. Gates](#---step-7-calibrating-individual-gates)
- [Calibration Storage](#---calibration-storage)

*\[This guide was adapted from the [Happy Hare Wiki](https://github.com/moggieuk/Happy-Hare/wiki) for ERCF v2. Thanks Moggie!\]*

This discussion assumes that you have setup and debugged your [Hardware Configuration](https://github.com/Enraged-Rabbit-Community/ERCF_v2/blob/master/Documentation/Hardware-configuration-checks.md).

Before using your ERCF you will need to calibrate it to adjust for differences in components used on your particular build. Be careful to calibrate in the recommended order because some settings build and depend on earlier ones. Happy Hare now has automated calibration for some of the traditionally longer steps and does not require any Klipper restarts so the process is quick and painless.

Upon starting your printer, you should be greeted by a large warning on your console:

```yml
Prerequsite calibration steps are not complete:
Use MMU_CALIBRATE_SELECTOR to calibrate selector for gates: 0,1,2,3,4,5,6,7
Use MMU_CALIBRATE_GEAR (with gate 0 selected) to calibrate gear rotation_distance on gate: 0
Use MMU_CALIBRATE_ENCODER (with gate 0 selected)
Use MMU_CALIBRATE_GEAR (with gate selected) or MMU_CALIBRATE_GATES GATE=xx to calibrate gear rotation_distance on gates: 1,2,3,4,5,6,7
Use MMU_CALIBRATE_BOWDEN
```

Let's take care of that next!

## #f03c15 #c5f015 #1589F0 Calibration Steps

> [!IMPORTANT]  
> When calibrating the first time you must perform calibration in the prescribed order.  Once complete you can re-calibrate particular steps but remember that some calibration changes will cascade.  E.g. after calibrating the gear, you must recalibrate the encoder, the bowden and possibly all the `gear_rotation_distances`.  Generally you can re-calibrate the servo (step 1) selector (step 2) and the gates (step 7) at any time, but the gear, encoder and bowden must always be done in that order!

```mermaid
graph TD;
    Hardware_Working --> MMU_SERVO["2.MMU_SERVO<br/><span style='font-size:10px'>(if fitted)</span>"]
    Hardware_Working --> MMU_CALIBRATE_SELECTOR["1.MMU_CALIBRATE_SELECTOR<br/><span style='font-size:10px'>(if MMU has a selector)</span>"]
    MMU_CALIBRATE_SELECTOR --> MMU_CALIBRATE_BOWDEN
    MMU_SERVO --> MMU_CALIBRATE_GEAR["3.MMU_CALIBRATE_GEAR<br/><span style='font-size:10px'>(can use on every gate to set rotation_distance)</span>"]
    MMU_CALIBRATE_GEAR --> MMU_CALIBRATE_ENCODER["4.MMU_CALIBRATE_ENCODER<br/><span style='font-size:10px'>(if MMU has an encoder)</span>"]
    MMU_CALIBRATE_ENCODER --> MMU_CALIBRATE_BOWDEN["5.MMU_CALIBRATE_BOWDEN<br/><span style='font-size:10px'>(can use to set length on every gate)</span>"]
    MMU_CALIBRATE_BOWDEN --> MMU_CALIBRATE_GATES["6.MMU_CALIBRATE_GATES<br/><span style='font-size:10px'>(available if MMU has an encoder)</span>"]

    style Hardware_Working stroke-width:0px
    style MMU_SERVO stroke-dasharray: 5 5, stroke:#c5f015, stroke-width:2px
    style MMU_CALIBRATE_SELECTOR stroke-dasharray: 5 5, stroke:#c5f015, stroke-width:2px
    style MMU_CALIBRATE_ENCODER stroke-dasharray: 5 5, stroke:#1589f0, stroke-width:2px
    style MMU_CALIBRATE_GATES stroke-dasharray: 5 5, stroke:#1589f0, stroke-width:2px
```
<!--
```mermaid
graph TD;
    LINEAR_SELECTOR["If MMU has Selector"]
    ENCODER["If MMU has Encoder"]

    style LINEAR_SELECTOR stroke-dasharray: 5 5, stroke:#c5f015, stroke-width:2px
    style ENCODER stroke-dasharray: 5 5, stroke:#1589f0, stroke-width:2px
```
-->

- For ERCF, Happy Hare keeps a `rotation_distance` on each gate which requires separate measured calibration of each gate, using `MMU_CALIBRATE_GEAR` or, using the encoder, with `MMU_CALIBRATE_GATES` to automate the process. This is important even if the drive gears are from the same vendor look similar. 

> [!TIP] 
> All of the calibration commands can be run in a "check/test" mode. Simply add `SAVE=0` to the command and the calibration will be run but the results will not be saved. This is very useful to practice or to verify calibration.

### #f03c15 #c5f015 #1589F0 Step 1. Calibrate your servo

Now it's finally time to install the servo arm!

Run the command `MMU_SERVO POS=down`. This will set the servo to the initial down position while you attach the servo arm.

Attach the servo arm, at about 90 degrees, perpendicular to the servo body. *Be careful not to twist the Servo splines while adding the arm - if you do, stop and run the previous command again!* Add the servo arm screw.

Next, tighten down the M3x10mm BHCS that clamps the servo arm down on the servo drive shaft splines. This will make an impression of the splines, locking the servo arm in place.

Happy Hare sets up theoretically good servo postions during installation, however they should be calibrated. ERCF *requires* precise servo calibration to work correctly. To get that precision, you need to run through this process to update and record the correct angle for the `UP` position. Refer to the pictures below to see what each of the servo arm positions should look like.

```yml
MMU_SERVO POS=up
  (Assume the position isn't quite right)
MMU_SERVO
Current servo angle: 125, Positions: {'down': 110, 'up': 125, 'move': 110}
  (Without arguments you can view the current angles)
MMU_SERVO ANGLE=128
  (Tweak until you are happy with the "up" position as compared to the picture below)
MMU_SERVO POS=up SAVE=1
  (Save the current angle (128) for the "up" position)
```

Repeat for the other two positions (`DOWN` and `MOVE`).

> [!NOTE]  
> Servos have a limited range of rotation. If you are unable to attain the servo angle required you might need to reposition the servo arm on the servo, or edit the servo configuration in `mmu_hardware.cfg`
 
**Servo positions on ERCF**

Make sure the `MOVE` and `UP` positions of your servo arm are set so that the arm does not hit the tophats when the selector is moving. See picture below to see where the servo arm should be for the 3 positions.

- Servo Up. This position releases the filament trap for printing without sync mode.

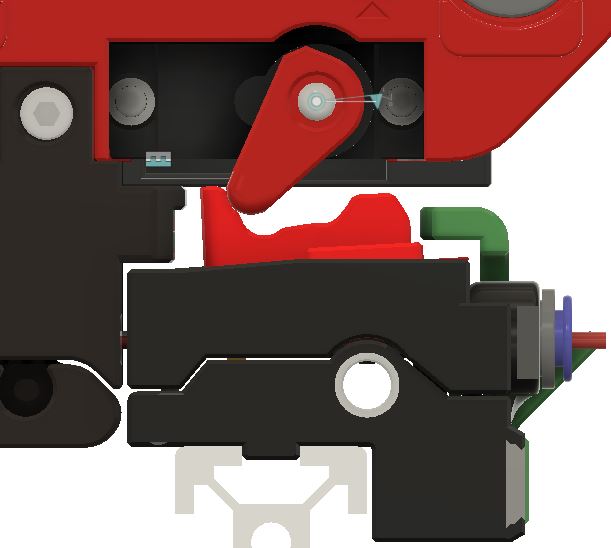
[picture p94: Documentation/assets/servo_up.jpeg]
Servo Up


- Servo Move. This position activates the filament trap so that the Selector can move.

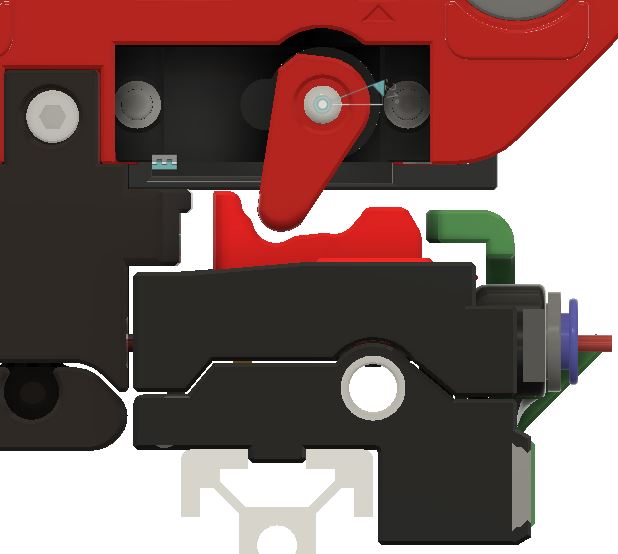
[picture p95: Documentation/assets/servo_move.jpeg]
Servo Move


- Servo Down. This position meshes the BMG gears to push filament. The filament trap is released to allow for Load/unload or to print with sync mode)

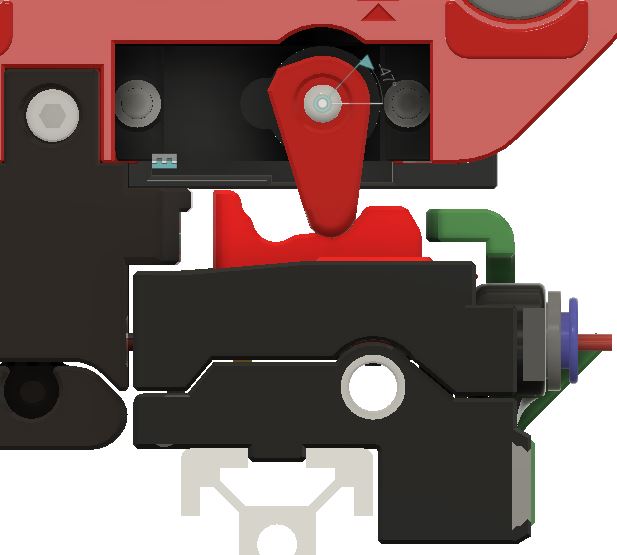
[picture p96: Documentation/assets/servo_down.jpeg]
Servo Down


**If the servo angles are set incorrectly, the servo will struggle to reach the angle set, which will reduce the servo's lifetime, and may even burn the servo out! You will know if the servo is struggling to reach position because it will keep buzzing while it tries to reach the set angle.**

> [!NOTE] 
> It is normal for the Gear motor to move back and forth slightly during a `MMU_SERVO POS=down` command. This is to ensure that the BMG gears mesh properly.

Once you are satisfied with your angles, you are done with this step!

### #f03c15 #c5f015 #1589F0 Step 2. Calibrate selector offsets

First, make sure that there is room between the endstop and Gate 0. We don't want the endstop to be activated while using Gate 0, instead we want there to be at least a 1.0mm gap between the two positions. If the endstop is activated when using Gate 0, you need to tighten the endstop adjustment screw (the BHCS on the Encoder). If for the endstop isn't activating even at the end of travel, the endstop adjustment screw needs to be loosened. The screw has a pitch of 0.5mm, so one full turn will move it in or out 0.5mm.

Once you have the endstop distance adjusted, There are three ways to calibrate the selector offsets:

#### A) Fully automatic calibration
Let's start by getting the selector cailbrated in this easy step (it is important to do this early because the bowden and gate calibration need to be able to select gates). This sets up the position all of all the gates as well as the bypass position if fitted. Firstly ensure MMU motors are off by running `MMU_MOTORS_OFF` and remove filament from gate #0 -- you may need to run `MMU_SERVO POS=up` to release the filament. Then re-insert and remove filament through selector to ensure that gate #0 is correctly alined with selector. Be careful and move the selector side to side whilst moving the filament inside the gate. Try to assess where the filament is centered in the gate and leave the selector in that position. Then run:

  > MMU_CALIBRATE_SELECTOR

Sit back and relax. The selector will move to find the extremes of movement and then use information about the geometry of the particular MMU and version/options you are using to generate and save the selector offsets automatically!

#### B) Extrapolate first and last gates
Although the automated method above will attempt to calibrate the Selector, it can result in drift unless all the gates/lanes are perfectly tight together. To address this a better method that can be used with ERCF v2 is as follows:
```yml
MMU_MOTORS_OFF
  (Use a piece of filament to align gate 0; remove filament)
MMU_CALIBRATE_SELECTOR GATE=0
MMU_MOTORS_OFF
  (Use a piece of filament to align the last gate; remove filament)
MMU_CALIBRATE_SELECTOR GATE=n
  (where n is the last gate number, remember we are 0 based)
```
This will automatically set the offset of all intermediate gates distributing any build variance

#### C) Individual gate calibration
Although it should not be necessary other than for the bypass gate, there is an option update a single position if you would like to tune or run into problems. See the command reference for more detailed information on options, but basically, you turn MMU motors off, line up the desired gate with the selector and run:

  > MMU_CALIBRATE_SELECTOR SINGLE=1 GATE=...

Strictly speaking `SINGLE=1` is only required if calibrating just your final gate to avoid automatic extrapolation.

#### C part 2) Bypass gate calibration
ERCF has a built-in bypass gate. Similar to the above step, you can calibrate it's position by aligning the selector and running:

  > MMU_CALIBRATE_SELECTOR BYPASS=1

**Validation:** At the end of this step you should be able to select any tool/gate on your MMU. For instance, try running `MMU_HOME TOOL=3` to re-home and select tool/gate #3.

### #f03c15 #c5f015 #1589F0 Step 3. Springy Calibration

*You should start with the Springy adjustment bolt only just touching the Spring Cap part, with little to no tension on the spring.*

Put a scrap of PTFE into Gate 0. Run the command `MMU_SELECT GATE=0`.

Feed a **new** piece of filament at least 250mm long into Gate 0 and past the encoder.

Run the command `MMU_TEST_GRIP`

Pull on the filament in the unloading direction. The gears should grip the filament and move the entire Drive Shaft as you pull. 

If the filament slips on the gears at all, tighten the Springy tensioner bolt, half a turn at a time, until the filament is fully and firmly gripped by the drive gears when you pull.

If the grip is too strong, eg. the filament is being mangled by the gears, or the filament is grinding, back off the Springy tensioner bolt half a turn and test again.

It is important to set the Springy tension correctly so that the drive gears have good grip on the filament. If this is not set correctly, later calibration steps may give erroneous readings, because the length of filament sent by the Gear Motor is used in the calibration calculations.

The Springy spring tensions the Servo downward, while still allowing the Servo to flex upwards slightly as necessary during operation.

### #f03c15 #c5f015 #1589F0 Step 4. Calibrate your gear stepper
**It is Very Important to get this right!**

In this step you are ensuring that when the gear stepper is told to move 100mm of filament it really does move 100mm.  It is akin to what you did when you set up your extruder rotational distance, although in this case no Klipper restart is necessary!  Select gate #0 (you can use `MMU_SELECT GATE=0` if you have finished the selector calibration above) and put some filament through the gate so that it pokes out just past the selector exit.  Run the following to ensure the filament is gripped if your MMU needs to actuate a servo to grip filament:

  > MMU_SERVO POS=down

Next remove the bowden tube and cut the filament flush with the ECAS connector at the output of the MMU (e.g the encoder on the ERCF design). Run this command to attemp to move 100mm of filament:

  > MMU_TEST_MOVE MOVE=100

Get out your ruler and very carefully measure the length of the emited filament.  Hold your ruler up to the bowden and gently pull the filament straight to get an accurate measurement. Next run this specifying your actual measured value (102.5 used in this example):

  > MMU_CALIBRATE_GEAR MEASURED=102.5

```
    Gear stepper 'rotation_distance' calculated to be 23.117387 (currently: 22.9)
    Gear calibration for gate 0 has been saved
```

> [!TIP]  
> You can also measure over a different length by using something like `MMU_TEST_MOVE MOVE=200` and `MMU_CALIBRATE_GEAR LENGTH=200 MEASURED=205.25` for a 200mm length for example. Don't forget the `LENGTH=200` argument, or it the calibration calculation will default to 100mm and set your gear calibration wrong!

> [!IMPORTANT]
> The value for `rotation_distance` should be between 22 and 24 for BMG gears - if you get a `rotation_distance` far outside of these values, something has likely gone wrong! Redo this step. Common mechanical causes include overtensioned Selector belts and misaligned Selector positions.

**Validation:** If you want to test, snip the filament flush with the ECAS connector again and run `MMU_TEST_MOVE`.  Exactly 100mm should be moved this time.

You can either repeat this for all other gates, or you can shortcut and use `MMU_CALIBRATE_GATES` in Step 7.

### #f03c15 #c5f015 #1589F0 Step 5. Calibrate your encoder

The next step is to calibrate the Encoder so it measures distance accurately. Re-fit the bowden to the encoder output. Alternatively, just make sure you have at least 500mm of filament at gate #0 before starting. Now run:

  > MMU_CALIBRATE_ENCODER

You will see an output similar to:

```
    Calibrating over 400mm...
      + counts: 368
      - counts: 368
      + counts: 369
      - counts: 369
      + counts: 369
      - counts: 369
    Load direction:   mean=368.67 stdev=0.58 min=368 max=369 range=1
    Unload direction: mean=368.67 stdev=0.58 min=368 max=369 range=1
    Before calibration measured length: 394.47mm
    Calculated resolution of the encoder: 1.085049 (currently: 1.094543)
    Encoder calibration has been saved
```

> [!NOTE]  
> (i) Use fresh filament - grooves from previous passes through extruder gears can lead to slight count differences.
> (ii) Make sure the selector is aligned with the gate. If it is off to one side you will almost certainly get dissimilar counts in forward and reverse directions.
> (iii) You want the counts on each attempt to be the same or very similar but don't sweat +/-3 counts.  Between the spring-tensioned servo and Binky encoder design they should be very consistent ;-)
> (iv) You can run this (like all calibration commands) without saving the result by adding a `SAVE=0` flag.

If this step worked then you should be able to unload the residual filament with `MMU_UNLOAD`. If you aren't happy with results, leave the filament ready for the next run and repeat this section.

### #f03c15 #c5f015 #1589F0 Step 6. Calibrate bowden length

Here you can calibrate the length of your bowden from MMU gate to extruder entrance. This is important because it allows the MMU to move the filament at a fast pace over this distance before getting to the more complicated part of the load sequence. To speed up this process, and depending on what sensors you have fitted for extruder homing, you may need to give the calibration routine a hint of how far way the extruder is.

There are different ways to do this depending on your configuration and sensor options:

1. If `extruder_homing_endstop: extruder` (or `mmu_gear_touch` or `filament_compression`), then you have a homing endstop and you can simply specify a `BOWDEN_LENGTH` that is GREATER than your estimated length to give plenty of room to find the homing stop.

  > MMU_CALIBRATE_BOWDEN BOWDEN_LENGTH=1500

2. If you are using `extruder_homing_endstop: collision`, then the `BOWDEN_LENGTH` supplied MUST be slightly shorter than the actual length. A good rule of thumb is to manually measure the distance from exit from the selector to the entrance to your extruder. Subtract 40-50mm from that distance. I measured approximately 690mm on my system, so will supply 650mm as the starting value. For example:

  > MMU_CALIBRATE_BOWDEN BOWDEN_LENGTH=650

```
    Homing MMU...
    Tool T0 enabled
    Calibrating bowden length from reference Gate #0
    Tool T0 enabled
    Heating extruder to minimum temp (200.0)
    Finding extruder gear position (try #1 of 3)...
    Pass #1: Filament homed to extruder, encoder measured 683.5mm, filament sprung back 3.2mm
    - Bowden calibration based on this pass is 683.5
    Finding extruder gear position (try #2 of 3)...
    Pass #2: Filament homed to extruder, encoder measured 682.7mm, filament sprung back 3.2mm
    - Bowden calibration based on this pass is 682.7
    Finding extruder gear position (try #3 of 3)...
    Pass #3: Filament homed to extruder, encoder measured 683.9mm, filament sprung back 3.2mm
    - Bowden calibration based on this pass is 683.4
    Recommended calibration reference is 680.2mm. Clog detection length: 16.8mm
    Bowden calibration and clog detection length have been saved
```

3. Finally, if you run into problems with collision detection at the extruder, you can run manual calibration. To do this, select gate 0, push filament through manually all the way to the extruder gears. This run `MMU_CALIBRATE_BOWDEN MANUAL=1` option. This will measure the distance in reverse to the gate homing position:

  > MMU_CALIBRATE_BOWDEN BOWDEN_LENGTH=1000 MANUAL=1

This will reverse home to the gate and uses Klipper's measurement of stepper movement.

> [!NOTE]  
> (i) This calibration assumes that the selector has been calibrated first.
> (ii) This may cause the extruder to be heated. This is to ensure that the extruder motor is energized and can resist the impact of the collision with the filament

### #f03c15 #c5f015 #1589F0 Step 7. Calibrating individual gates

This step allows for calibrating slight differences between gates and saves you from having to use `MMU_CALIBRATE_GEAR` on every gate. Even with ERCF this is optional because if not run, the gates will tune themselves as they are used automatically!  That said it be beneficial to get this out of the way with a test piece of filament, but doing it also: (i) removes the need to set the `autotune_rotation_distance` in `mmu_parameters.cfg`, (ii) is necessary if there is substantial variation between gates -- e.g. if BMG gears for different gates are sourced from different vendors.

Simply make sure filament is available at the gate you want to calibrate (you can also insert a 500mm piece of filament) and run:

> MMU_CALIBRATE_GATES GATE=1

You will see an output similar to:

```
    Tool T1 enabled
    Calibrating gate 1 over 400.0mm...
      + measured: 404.4mm
      - measured: 404.4mm
      + measured: 404.4mm
      - measured: 404.4mm
      + measured: 405.5mm
      - measured: 405.5mm
    Load direction:   mean=404.7 stdev=0.63 min=404.4 max=405.5 range=1.1
    Unload direction: mean=404.7 stdev=0.63 min=404.4 max=405.5 range=1.1
    Calibration move of 6x 400.0mm, average encoder measurement: 404.7mm - Ratio is 1.011872
    Calculated gate 1 rotation_distance: 22.941324 (currently: 22.672165)
    Calibration for gate 1 has been saved
```

> [!NOTE]  
> (i) You can also quickly run through all gates (and even pass the loose filament gate to gate) with `MMU_CALIBRATE_GATES ALL=1` <br>
> (ii) If you see "Calibration ignored because it is not considered valid (>20% difference from gate 0)" then it either means the calibration failed because filament was not moving correctly, or the encoder was not working correctly. Less likely but possible is because you have not calibrated gate 0 (`MMU_CALIBRATE_GEAR` and `MMU_CALIBRATE_ENCODER`) correctly which serves as the reference gate.

> [!IMPORTANT]
> The value for `rotation_distance` should be very close to the `rotation_distance` from step 4 - if you get a `rotation_distance` that is very different, something has likely gone wrong! Redo this step. Common mechanical causes include overtensioned Selector belts and misaligned Selector positions.

### #f03c15 #c5f015 #1589F0 Calibration Storage
All calibrated results are stored in the configured `[save_variables]` file. By default and most usually this will be `mmu_vars.cfg`. Here is a list of those variables and the command that sets them:

  | Variable | Command | Notes |
  | -------- | ------- | ----- |
  | mmu_servo_angles | MMU_SERVO | E.g {'down': 45, 'up': 125, 'move': 110} represents the angles for the three servo positions |
  | mmu_gear_rotation_distances | MMU_CALIBRATE_GEAR or MMU_CALIBRATE_GATES | The list represents `rotation_distance` for each gate |
  | mmu_encoder_resolution | MMU_CALIBRATE_ENCODER | The distance each encoder signal transition represents |
  | mmu_selector_offsets | MMU_CALIBRATE_SLECTOR | A list of offsets for each gate of the MMU |
  | mmu_selector_bypass | MMU_CALIBRATE_SELECTOR | The offset of the bypass (passthough) location |
  | mmu_calibration_bowden_home | MMU_CALIBRATE_BOWDEN | Records the gate homing endstop used as a basis for the calibration |
  | mmu_calibration_bowden_lengths | MMU_CALIBRATE_BOWDEN | The list will be the same length as the number of gates on your MMU |
  | mmu_calibration_clog_length | MMU_CALIBRATE_BOWDEN | Only used with encoder although always set incase you add in the future |

Happy Hare documentation lists all [Calibration Commands](https://github.com/moggieuk/Happy-Hare/wiki/Command-Reference#---calibration)
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

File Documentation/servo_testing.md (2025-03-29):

**The following is an unedited log of the testing that Marc performed on various servos over the course of a few months. All I've done is copy every post he made about servos, along with the the images he posted. I also added some of the questions we asked him during testing, for context.**

i whipped up a test setup and tortured a random MG90 today, will repeat the test with savox, guo hua and metal gear mg90 tomorrow evening

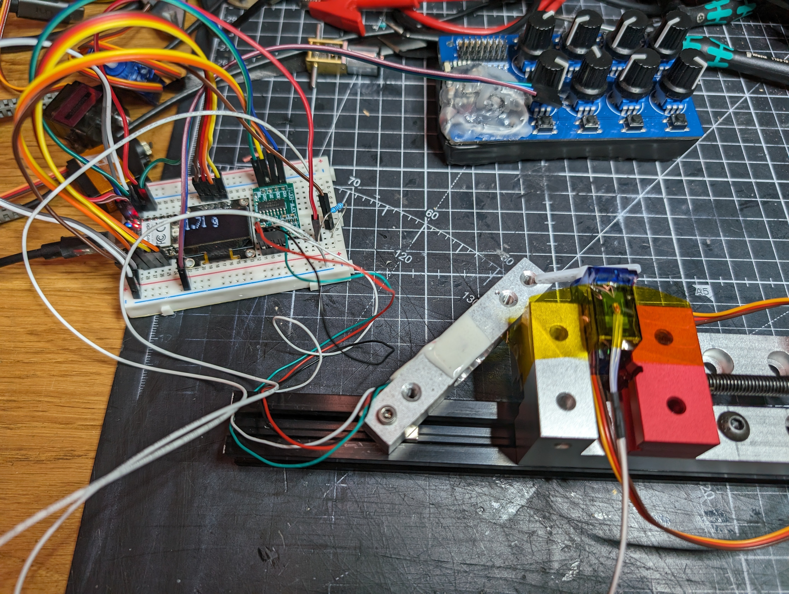
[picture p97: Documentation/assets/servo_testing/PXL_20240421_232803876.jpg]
Servo Test Rig


after ~45 "hard push" actions in short succession (100ms delay between each try) the MG90 is basically about to fail and already started to degrade push performance after 25 pushes

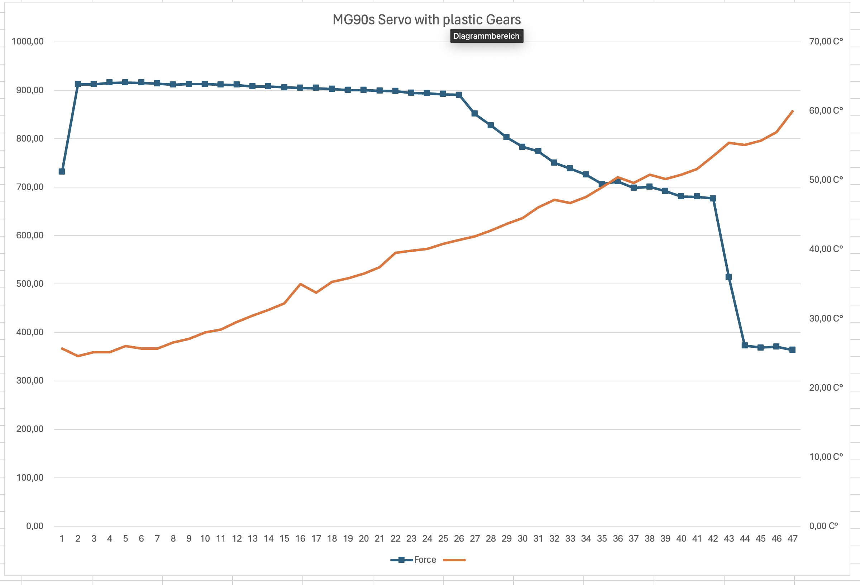
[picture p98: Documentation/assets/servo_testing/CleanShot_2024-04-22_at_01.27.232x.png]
MG90s Servo with Plastic Gears Results


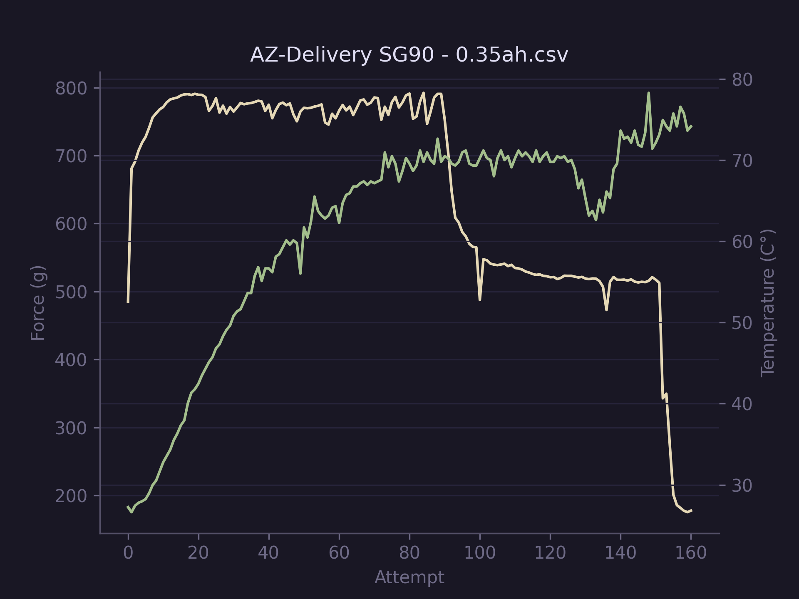
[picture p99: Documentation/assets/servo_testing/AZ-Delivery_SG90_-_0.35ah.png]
AZ-Delivery MG90 Results

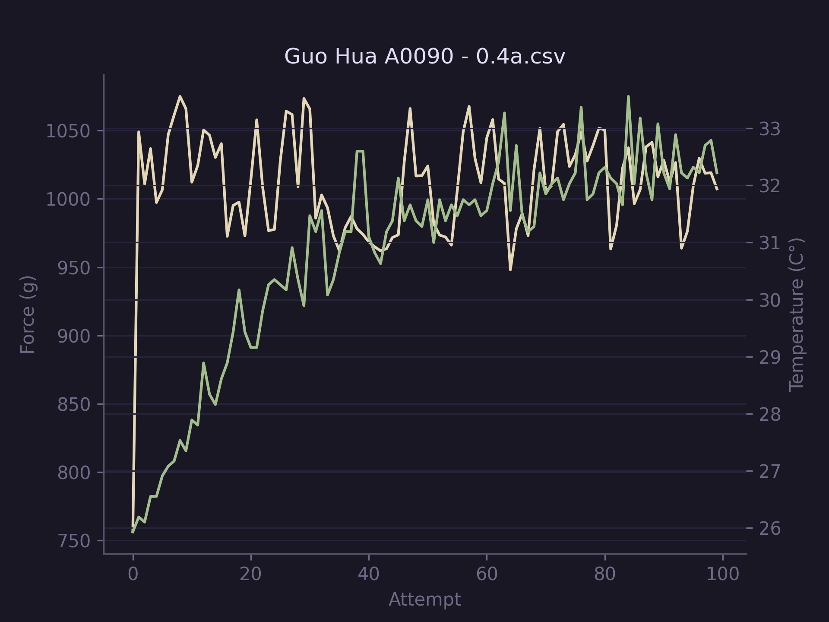
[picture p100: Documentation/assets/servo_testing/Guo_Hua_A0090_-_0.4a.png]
Guo Hua A0090 Results

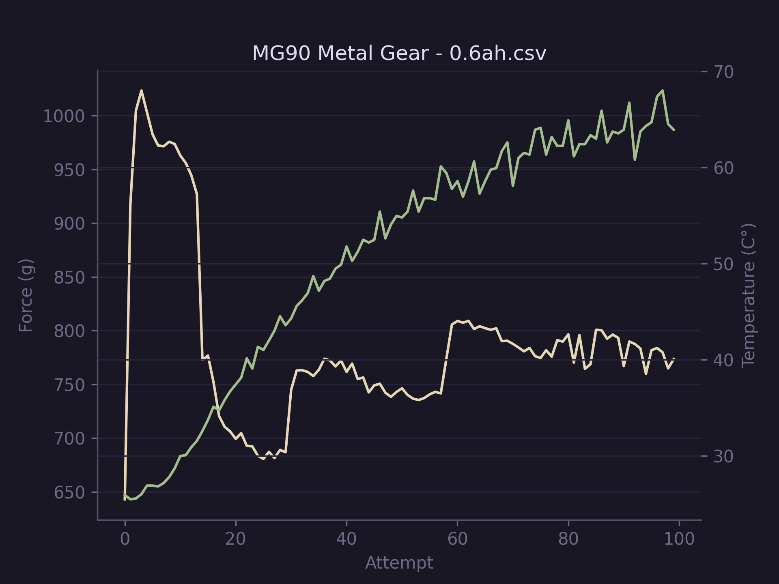
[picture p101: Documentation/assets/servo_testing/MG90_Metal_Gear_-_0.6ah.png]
MG90 Metal Gear Results

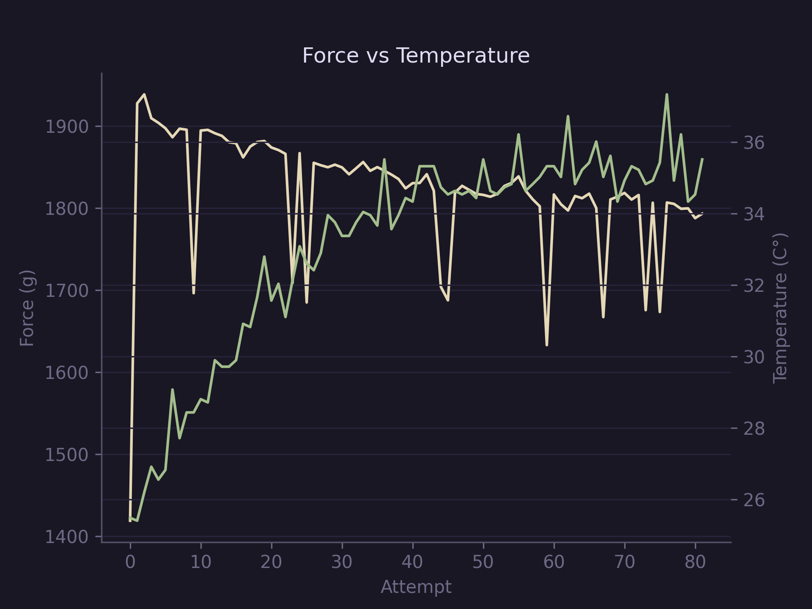
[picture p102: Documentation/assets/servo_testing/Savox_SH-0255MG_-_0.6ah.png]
Savox Force vs Temperature


and here's a comparison, solid lines are the force and dashed the temperature lines, same color same servo

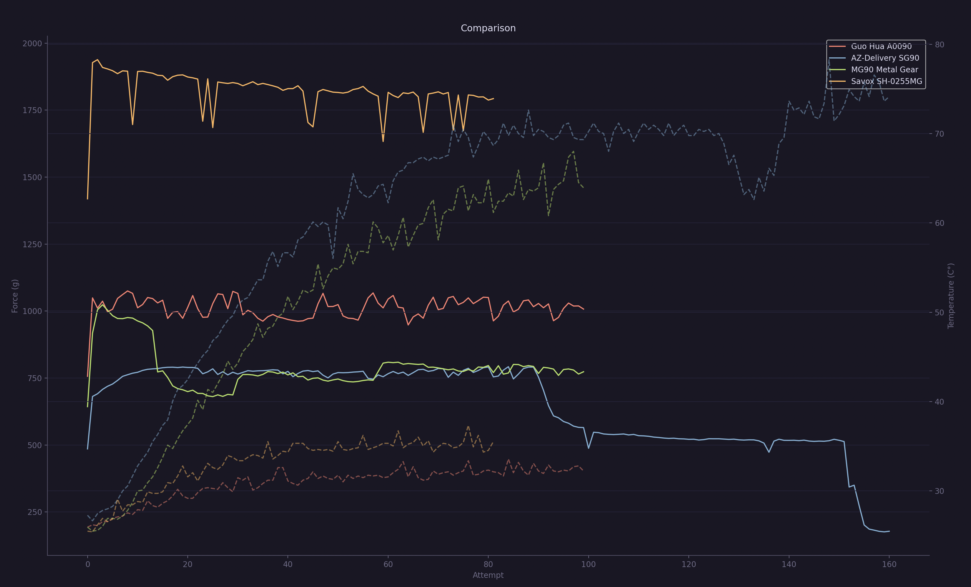
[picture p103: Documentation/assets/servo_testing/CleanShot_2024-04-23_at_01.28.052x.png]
Comparison


so, the Savox beats all others easily, the plastic gear one is really unreliable, the metal gear MG90 is kinda ok and holing on, the Guo Hua seems also pretty solid and stable, but far away form the push power of the savox.
all force and temperature values should be considered rough estimates, because i simply threw together a load cell and ntc temperature probe, but for comparing this is still valid data to see the difference
also, the Savox and Guo Hua stay quite cool, both MG90 variants get hot quick and can lead to permant failure easily when stressed a lot

Guo hua a0090 would be also an option, seems stable and reliable, but not ad strong as the mg90s

here's the gist of the Data i gather so far:

Results Data Table

the SG90/MG90 basically disqualify due to quick heat buildup, A0090 and SH-0225MG keep pretty cool, A0090 does have more push power than the MG90/SG90 but is far behing the SH-0255MG

i just ordered these for Servos for additional tests, give me a shout, if you know of any more i should/could include in these tests, i also ordered an original TowerPro MG90S, since i only got a random clone tested so far

GDW DS041MG (https://gdwservo.com/product/gdw-ds041mg-5kg-torque-metal-gear-micro-mini-digital-servo-for-450-helicopter-fix-wing-rc-auto-robot-arm/)

DSPower DS-S006M (https://www.dspowerservo.com/ds-s006m-metal-gear-9g-servo-micro-servo-product/)

JX Servo PDI-1109MG (http://www.jx-servo.com/en/Product/micro/MD/566.html)

Original TowerPro MG90S (https://www.towerpro.com.tw/product/mg90s-3/)

Servo Tuesday 1
Servo Tuesday 2

Seems to be a Servo Tuesday 

Will start testing tonight

TowerPro MG90S being stressed on the bench, maxes out at 740g so far and already quickly rose to 51.2°C, so far not looking better than the clones, will run through 3000 cycles with 1s pause in between 

well, already started to degrade when it rose to 55°C, so i canceled that run and put on the GDW DS041MG instead, lets see how it'll hold up, change to 5s instead of 1s pause in betrween cycles

GDW DS041MG (~7.5€ on AliExpress) put up a solid performance over night, stable ~800g of push force, quickly rose to ~30°C but didn't rise above 35°C which should be quite fine, this was 3000 attempts at 5s pause 

GDW DS041MG Results

some nerdy stuff, i completely redid the electronics for the test rig and switched form rp2040 to an esp32, so instead of logging to a serial console the data now flows directly into my influxDB which i have running on my HomeAssistant Server anyway. Usually that's a time based logging, but i programmed the esp32 so that the test run always starts at start of epoch and goes from there, so the data is comparable to each other over real timeframes

using that data i can use Grafana to dig in and plot it into graphs, and even publish snapshots to share online: https://snapshots.raintank.io/dashboard/snapshot/K923gpDqSMlkNJxxM6egWdj5cI3GKi1t

so, now i've got the JX PDI-1109MG on the Test bench, temperature looks good so far, similar to the GDW around 30-35°C, but push force seems to be almost 100g less than the GDW at mean:

JX PDI-1109MG (~6€ on AliExpress) kept going stable at the force and temperature over all 3000 attempts, so not as strong as GDW, but it seems to be stable for longer use 

JX PDI-1109MG Results

comparison in one graph of those 2

GDW DS041MG and JX PDI-1109MG Results

next up: CSPower 12G Digital Servo (~4€ on AliExpress)

CSPower 12G Digital Servo (~4€ on AliExpress) is off to a good start:

CSPower 12G Beginning

Servo Size Comparison

second from the right, right next to the original mg90s, a tiny bit smaller

CSPower 12G

i'll do another run with the original towerpro mg90 after this run, but at 1s pause it quickly heated up as well

will give it another chance at 5s like the others right now

yes, Guo Hua and Savöx standing above

will redo both on the latest rig and test firmware as well to have a fair comparison with 3000 tries 5s pause

takes about 5h for one test run 😅

which is also kind of a fair "test" for real world usage imho

i'm running these in a ~20°C room right now sandwiched between 2 aluminium blocks (vise), that should already enable some heat dissapation, now how would they handle in hotter climate?

especially in such cases MG90 might go bad quicker

ProModeler was difficult to source, right?

US only?

44$ and no shipping option to me, so, yea no thanks 😄

CSPower 12G is happily chopping on without signs of degradation:

CSPower 12G preliminary results

so, yea very solid performance for the price for the CSPower 12G Servo:

CSPower 12G results comparison

next i'm rerunning the Savöx as a comparison, already feels like they're playing in different leaques...

Savöx basically "shifts" that whole graph into a new perspective:

Savox results comparison

savöx is the green dot top left

1.53kg average currently

i mean, what really sets the savöx above from the others, is, that it basically doubles the push force of the others while also being the coolest to operate, really suprising considering how similar the others perform: 

would be curious to add ProModeler to the list, though i don't think it'll end up as the recommodation for most people, it'll be difficult to beat Guo Hua performance/price wise and the CSPower seems to be very good for that low price

Guo Hua is available for 6-7€ currently on AliExpress

ea, i'll slap on the guo hua again tomorrow morning, savöx will run for another ~4h

I'd currently group the servos into: 

discouraged: MG90 (Clones and Original)

budget options: CSPower, GDW, JX

default recommodation: Guo Hua

high peformance: Savöx (, maybe ProModeler)

so, Savöx performed very stable, 1560g push force mean and did't exceed 20.5°C, pretty impressive.

Guo Hua is running since this morning, kinda expected a bit more push force, but 776g is still a solid performance so far, pretty happy about the temperature, it's even below the savöx

Guo Hua Results Comparsion

actually you're right the temp of guo huo does not make sense, need to investigate, because this is the temp in the room for the last 24h:

Room Temp

i'd put out basically this: 

discouraged: MG90 (Clones and Original) [tests have shown degrading push power and thermal problems in stress tests]

budget options: CSPower 12g, GDW DS041MG, JX PDI-1109MG

default recommodation: Guo Hua A0090

high peformance: Savöx 0255MG (, maybe ProModeler)

will do, i'll investigate the guo huo temperature later tonight and add a final run of the original tower pro which is missing right now, then i'll announce that in the vendor chat with some data, prices, etc.

to be honest, i'm a bit confused right now, doing another test with another random XTVTX MG90 looks like this so far:

XTVTX MG90 preliminary results
XTVTX MG90 results comparison

will do at least one other XTVTX to compare

i am collecting voltage and current, but the sensors i have seem to be shit, so not really usable data

i can read about 0.254A on my lab power supply on this run currently

additionally connected to usb though, so probably not the full picture

the other XTVTX MG90 i tested did degrade after 1000-2000 tries:

XTVTX MG90 degradation

Maybe the other one was bad

Will try ~100 attempts with every clone i have to get a "range"

well, just came back from outside...

good impression didn't last:

XTVTX MG90 failure

VIDEO

Houston, we've got a failed MG90S clone

Yes, it was probably still "fresh" but went bad quick

Broken plastic gears

1 gear failed completely and one lost one tooth

should i try to destroy another? 😄

i put on the original TowerPro MG90s instead, let's see if it also shares that same fate

well, i'd say there's already kind of a trend visible:

TowerPro MG90S Trend Beginning

These are the original TowerPro MG90s.

`What good are these motors if they fail so badly. Must be for the very lightest toys.`

yea, especially because these 2 variants are basically the "only" servos you get when searching amazon for small servos:

can't get Guo Hua A0090, GDW DS041MG, JX PDI-1109MG or CSPower 12g on amazon here in germany

i need to source all of them from ali

trend does seem to continue:

TowerPro MG90S Trend continuing

seems to stabilize so far:

TowerPro MG90S stablized

i had to restart that test, the servo arm startet slipping/stripping out on that test (bottom graph), the new test was stable over 3000 attempts:

TowerPro MG90S stable?

so, overall the TowerPro Original did similar to the other good servos:

TowerPro MG90S Comparison

will slap a final clone on the bench to see if it also fails

still doing more tests on the MG90 clones, 2 did quite ok so far, one failed with brokes gears and the on on it right now quickly dipped in performance but is stable so far, but it does make a struggling sound, so might fail during this test :

XTVTX MG90 prolonged testing

short status quo, still testing, so far 5 XTVTX Servos, suprisingly most are putting up a good performance aside from the one that failed with broken gears and one (Number 4) which did not work at all, so it's missing in the graph:

XTVTX MG90 mixed bag

there is quite a bit variation in push force though

`The manufactured consistency sounds like a big issue to me despite the performance`

yea, currently i'd still recommend one of the others, kinda expected number 3 to fail as well, it was very noisy, almost crying to be released from it's misery, while pushing

`yeah in my opinion 2 out of 5 being defective is horrible even before performance testing. In my opinion if it is any worse than 1% of 100 samples, that's hugely iffy.`

I'll do additional tests with the others as well to see how they stack up

`have you tested the GDW DS041MG as of yet?`

yes, worked pretty good:

GDW DS041MG results

the #7 of XTVTX MG90 did some funky stuff at the, will do another round for that one:

XTVTX MG90 #7 mixed bag

so, yea this #7 of the XTVTX MG90s really does some wonky stuff, (blue round 1, red round 2)

XTVTX MG90 #7 mixed bag

BTW, i've collected almost 50 000 force measurments by now 

`There are more GDW issues showing up on Facebook now too.`

i'll put on one of the other GDW after this MG90 testrun in ~1h

i got 4 GDX here i can test

#7 is really a weird one, expected it to completely fail, but seems like it'll go out with decent values, still the weird spikes  and variance of performance would disqualify it for me

XTVTX MG90 mixed bag

started testrun on GDW #2

GDW DS041MG #2 results

second GDW performt quite consistend, i think i've got the lever arm a bit further out which explains the differnt push force

#3 GDW is also performing similar to the #2 so far

`bad batch then, or is it bad software configuration I wonder?`

this only tests force + temperature currently

not speed

i'm waiting 100ms after initializing the move to measure

so, let's print a "batch" test jig 😅
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

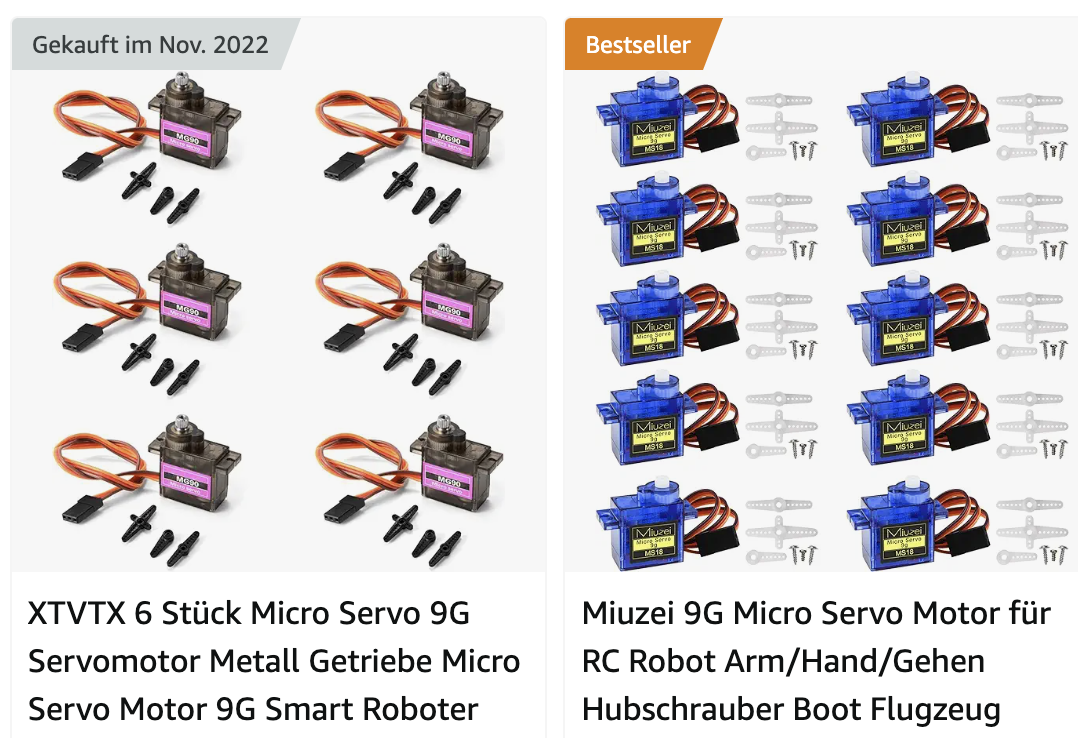
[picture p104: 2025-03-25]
Documentation/assets/servo_testing/CleanShot_2024-05-02_at_21.44.022x.png

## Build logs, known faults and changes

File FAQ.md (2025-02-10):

# ERCF v2 FAQ

### Q1. Will there be kits available for ERCF V2, and where can we get them?
LDO and  a number of vendors will have kits available for ordering in the coming months. Full kits will be available sometime in late 1st quarter of 2024.

### Q2. I bought an ERCF v1.1 kit. Will this be compatible?
ERCF v1.1 kits will be compatible with V2 with some additional hardware and fastener kits. We have made every effort to utilize as much of the original kit as possible. Upgrade kits will be available at various select vendors in the coming months. Be aware the kits will be less a single channel for the V2 upgrade to accommodate the wider filament blocks.

### Q3. Will ERCF come with a filament cutter?
ERF (Enraged Rabbit Filametrix) has been developed and optimized to work with ERCF V2. Although dozens of toolhead designs exist, the initial launch will be based on the Voron Stealthburner with Clockwork 2. There are numerous versions of toolheads, and the library of STLs will be expanding to support the greater community. We also encourage the public to develop and test their versions and to submit them to be included in our collection. More extruders are being actively developed and will be released in the coming months.

### Q4. I see that ERCF comes with a built-in buffer. Is this required or optional?
Enraged Rabbit Cotton Tail (ERCT) has been specifically designed to give the best multi-filament experience for V2; however, it is completely modular and optional for your build. You can choose to use other buffer designs; our software design is flexible. One of the stand-out features of ERCT is the ability to use a pre-gate sensor, which is designed specifically to improve Endless Spool performance.

### Q5. Do I have to order a kit, or can I self-source this? Is there a BOM?
Kits are expected to be available in the 1st quarter of 2024. Our BOM will list all the parts needed with a wizard to help you customize the kit to your requirements. The BOM will be found through our GitHub listing with links to vendors who can provide parts for self-sourcing.

### Q6. When and where will the v2 BOM be located? Is it with the same BOM as V1.1?
The V2 BOM will located on the GitHub page after RC1 has been released. This will be at a new location, not the old ERCF V1.1 site.

### Q7. What tool heads will this support?
Initially, ERCF V2 will be released with ERF (Filametrix) for Voron Stealthburner CW2 toolheads. Active development and collection of many popular hotends to companion with it is underway and will be part of the GitHub Repository. Alternative extruders are also being developed or being sourced with a cutting head. ERCF V2 also supports sensorless systems but is less reliable than a filament-cutting solution.

### Q8. Is the BTT MMB board required, or will older Easy BRD still work with V2? 
BTT MMB is the new standard and recommended board for V2. Easy BRD and alternatives will work for most of V2's features, but some of the new features, like pregate sensors and, in some cases, RGB lighting, will require a board with enough endstop and LED inputs to operate fully.

### Q9. Where can I get support for my ERCF V2 build?
ERCF V2 is built on a community of supporters and other experienced builders. Visit the [ERCF Discord server](https://discord.gg/MPZ4cHm9gm) for any questions and support issues, where members the community are there to help.

### Q10. Is there a build guide on assembling and calibrating my new ERCF?
Yes, a build guide is available in PDF format on the GitHub repository.

### Q11. Will ERCF V2 work with other non-Voron printers?
ERCF V2 currently works with most Klipper-based printers. The current exceptions are sandboxed builds of Klipper made proprietary by some companies and do not have the ability to add third-party software. Consult your product's support pages to see if there are ways to add third-party add ons, which may allow you to install the necessary software for ERCF V2 to work with your printer.

### Q12. I modified by V1.1 with TripleDecky, SturdyBunny, Springy, etc.  Do I already have a ERCFv2?
No. While ERCFv2 incorporates many "beta" modification projects from the team, it also includes many refinements, some subtle and some not.  These changes were all necessary to guarantee ERCFv2 would work together.  The only exception to this is that TripleDecky C7.0 filament blocks are identical to those in ERCFv2.  Other than those you are strongly encouraged to reprint and re-build to ensure you have a supported platform. In addition Happy Hare, with a vendor and version set to "ERCF" and "2.0" will correctly support ERCFv2 but this mode will not necessarily work with a heavily modified v.1.

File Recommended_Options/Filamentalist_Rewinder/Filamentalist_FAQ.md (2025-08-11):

# Filamentalist Frequently Asked Questions

[1. Troubleshooting](#troubleshooting)

[2. Dimensions/Footprint](#dimensions-footprint)

[3. Enclosure Solutions](#enclosure-solutions)

[4. Gear motor recommendations and 40 tooth mod](#gear-motor-options)

[5. Pregate Sensor Solutions](#pregate-sensor-solutions)

[6. Rubber Band Sourcing Options](#rubber-band-sourcing-options)

[7. TPU - Can the Filamentalist handle soft/flexible materials?](#flexible-filament)

## Troubleshooting
- If you have built the Filamentalist(s) and are having issues with its functioning such as loose loops or gear motor stalling please refer to this [Trouble Shooting Guide](https://github.com/SkiBikePrint/Filamentalist/blob/9d7a90dc3dec40c67051558c80c616155eb8eba8/troubleshoot.md).  If this doesn't help to resolve your questions you can get help from the many great users at the Filamentalist Discord server here (https://discord.gg/uDcGxukRKd)

## Dimensions Footprint
- Length:  186mm
  - Length with 200mm Diameter Spool:  202mm
- Height:  76mm without optional Base Plate, 79mm with Base Plate
  - Height with 200mm Diameter Spool:  252mm without optional Base Plate, 255 with Base Plate (varies slightly with Rim Roller rubber band thickness)
- Width:  80mm Axle Version = 81.5mm **(max spool width of 68mm)**, 100 mm Axle Version = 100mm **(max spool width of 86.5mm)** <br />
  <br />
    
[return to index](#filamentalist-frequently-asked-questions)

## Enclosure Solutions

  ### Filamentalist Enclosure

  An elegant passive enclosure/dry box (no heaters or fans) designed to house the Filamentalist passive rewinder.  It is great for a 4-6 channel ERCF (can go to higher channels if desired).  It consists of (4) printed endcaps, (6) pieces of 2020 extrusion cut/ordered to the desired length, and 0.060" (1/16') polycarbonate sheet(s) cut to size.  Details and files here:  https://github.com/SkiBikePrint/ERCF_Mods/tree/main/Filamentalist_Enclosure

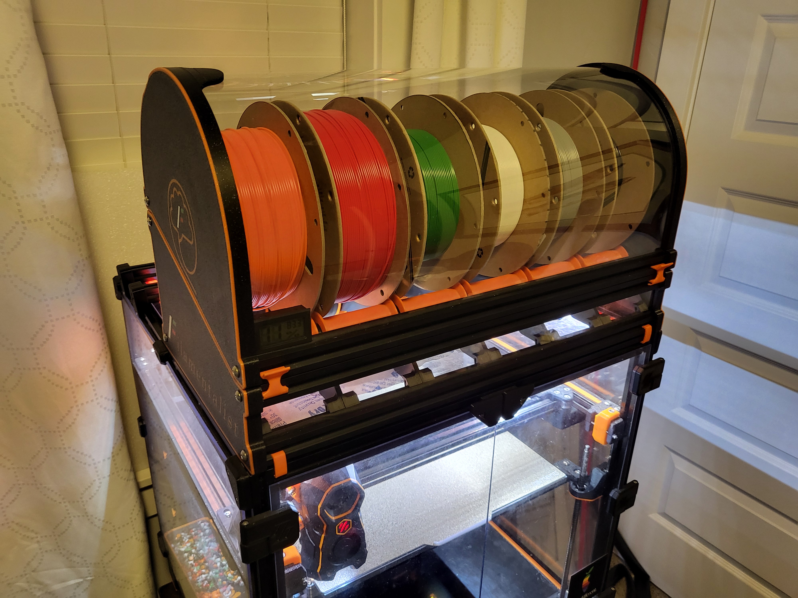
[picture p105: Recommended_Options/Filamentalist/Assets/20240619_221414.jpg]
  

  ### (Un)original Prusa Drybox

  Box is available here:  https://www.printables.com/model/551828-unoriginal-prusa-drybox .  Delete the rollers and add your own Filamentalist mounting solution.  You may need the rear load option for the Filamentalist

  
  (solution/picture courtesy of barsam on Discord)<br />
  <br />
    
  [return to index](#filamentalist-frequently-asked-questions)

## Gear Motor Options

  It is frequently asked if a NEMA 14 gear motor is strong enough to drive an MMU plus Filamentalist.  The 0.8A Moons NEMA 14 motor that came with my ERCF V1 Blurolls kit worked fine with the ERCF V1 and Filamentalist.  When I upgraded to ERCF V2 the additional resistance that came with the "Springy" version of the selector made the system slightly underpowered with a NEMA 14.  So if a NEMA 14 is what you currently have for your ERCF, TradRack, or other MMU, I suggest you try it before buying a higher torque motor.  If you are building a new MMU, then a NEMA 17 with torque greater than 40N-cm is recommended.  

  For the ERCF, Grafton's 40 tooth gear mod is also recommended ( https://www.printables.com/model/692720-ercf-40-tooth-gear-modifiction ). It allows you to use the same belt as is used with the baseline 80 tooth gear by providing a higher motor mount to take up the slack. Some ERCF kits come with a 42Ncm NEMA 17.  This combined with the 40T mod should give you sufficient torque to overcome MMU and long bowden tube resistance as well as allowing to run the Filamentalist at 300+mm/s speeds.  

  If you are buying a new NEMA 17, below are verified high torque motors (55-59Ncm) that perform well in the needed RPM range for 200-500mm/s load/unload speeds.  There is really no need to go higher than the 55-59Ncm torque range as you will just start grinding grooves in your filament with the MMU gear.  There is likely several other stepper motor options that have similar specifications.

1. 17HE19-2004S from stepperonline.com - 55Ncm (they have a new 17HS19-2004S1 50Ncm version that should be similar to the 17HE19-2004S but a little more powerful)
2. LDO-42STH48-2504AC - 55Ncm<br />
  <br />
    
  [return to index](#filamentalist-frequently-asked-questions)

## Pregate Sensor Solutions

  Research the options below and decide what will work best for you.
  
  ### CottonTail Lite:  
  - https://github.com/Tyler8299/CottonTail-Lite
  - Includes:
    - Coupler Blocks
    - End Cap Mount 
    - End Arm Cap Mount
    - End Arm Cap Mount Extension
    - Universal Electronics Box, Lid, and Mount
    - LED Carrier/Apron
  
  

  ### CheeseFrog's
  https://github.com/juliusjj25/ERCF-Pregate-Sensors

  This is what SkiBikePrint uses (SkiBikeMake (Filamentalist) on Discord).  It is simple and works great.  It requires the "bumped" simulated roller lever style Omron D2F-L3 microswitches.  These are great for a new build.  Retrofitting this onto an existing ERCF requires a tear down of the unit to replace the filament path portion of the blocks as well as the latches.  I did it the brute force way and trimmed my existing latches back with clippers and "muscled" the filament path parts out and back in to the blocks.  The brute force approach may not be for everyone!
  
  

  ### Gneu42's Filament Block 
  https://github.com/gneu42/Triple-Decky/tree/main/STL/ERCF-V2/Rev_C/Rev_C9/Optional%20Pre-gate%20Sensor%20(Experimental)

  Similar to the CheeseFrog solution but more complex.  Also requires a teardown/rebuild if added to an existing ERCF.<br />
  <br />

  ### Filamentalist Tensioner Mount based Pre-Gate Sensors

  This option is provided for users who are using an MMU other than ERCF and don't have another option for pre-gate sensors.  Although these work well, I have found that having the sensor "bump" at the beginning of the Tensioner Mount filament path makes filament loading a little more difficult.  If you are building a new ERCF I recommend the Cheesefrog sensors above.  If you have an existing ERCF and have the space for them, the CottontailLite sensors above are a good option.  For more information on the Tesnioner Mount based pre-gate sensor option refer to the assembly manual, CAD, and stl files.

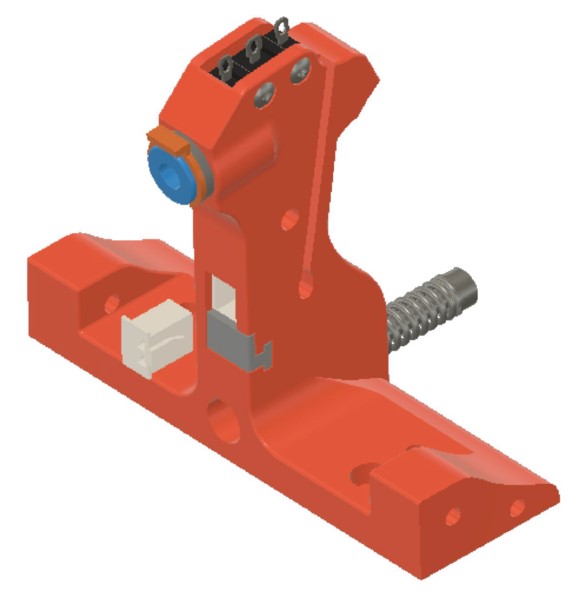
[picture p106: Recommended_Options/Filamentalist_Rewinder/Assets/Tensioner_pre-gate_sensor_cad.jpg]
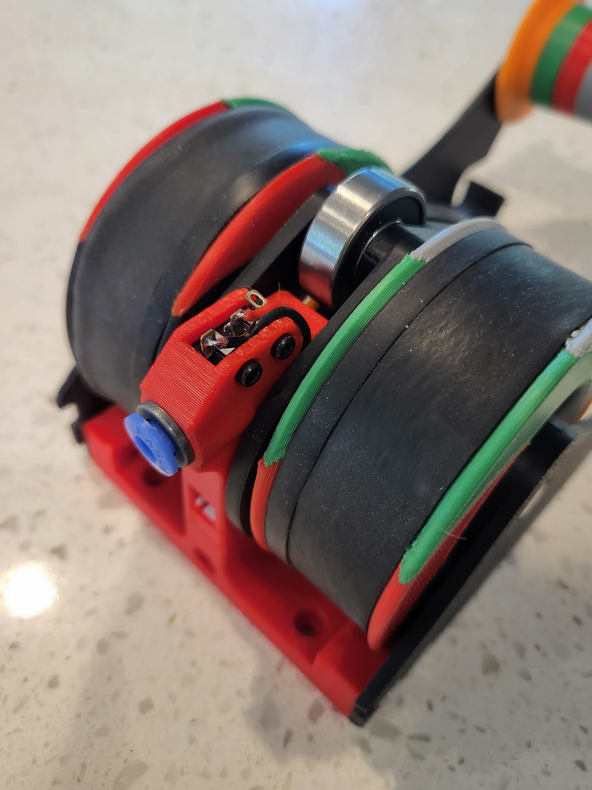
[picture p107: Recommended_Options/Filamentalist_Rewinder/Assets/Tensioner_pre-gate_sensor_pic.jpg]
  

  [return to index](#filamentalist-frequently-asked-questions)

## Rubber Band Sourcing Options

### Bike Tire Inner Tube
- You can cut to get a perfect fit across the face of the Rim Roller for 80mm, 100mm, or custom width rewinders with this solution.  Mountain bike or "balloon" tire sized tubes for tires in the 1.75"-2.5" width work well.  Select a wheel diameter of at least 16" to have enough material for up to 12 100mm wide rewinders.  Cut at ~30-35% wider than face of Rim Roller to account for width reduction when stretched onto roller.
  - easy to source locally (your garage, bike shop, hardware store,...)
  - Amazon example: https://www.amazon.com/BELL-Standard-Bicycle-Inner-Tube/dp/B003CUBPUY
  - Aliexpress example: https://www.aliexpress.us/item/3256804654544066.html
 


### Rubber Bands
  - For the standard size Classic Rewinder (20mm Rim Roller face width):
    - Size #82 (2 1/2" length x 1/2" wide) or ~50mm diameter (~80mm length) x 10mm width
      - qty 2 per roller for 80mm width version, qty 3 per roller for 100mm width version
    - Amazon example: https://www.amazon.com/AIWOQI-Industrial-supplies-Survival-Tactical/dp/B0CZQ57TF6
    - Aliexpress example: https://www.aliexpress.us/item/3256803949130763.html
  - For the standard size FV3 Rewinder (23mm Rim Roller face width):
    - Size #84 (3 1/2" length x 1/2" wide) or ~57mm diameter (~90mm length) x 12-13mm width
      - qty 2 per roller for 80mm width version, qty 3 per roller for 100mm width version
    - Amazon example: https://www.amazon.com/dp/B0CBJQLXLB
    
<br />
  <br />
    
  [return to index](#filamentalist-frequently-asked-questions)

## Flexible Filament
  - The Filamentalist has been successfully tested with 95A hardness TPU
  - 85A hardness TPU (for example NinjaFlex) - NOT RECOMMENDED! - Soft TPU tends to kink and jam during unload.
  - The smaller/lighter the spool, the better.  The resistance created by the rotational inertia of a heavy spool can cause the Flexibile filament to kink at the o-rings or just expand and jam in the tubing.
    - the little 200/250 gram spools work great.
    - Lower unload acceleration reduces the above problem by reducing the rotational inertia.<br />
  <br />
    
  [return to index](#filamentalist-frequently-asked-questions)

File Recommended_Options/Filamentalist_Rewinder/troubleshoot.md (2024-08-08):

# Filamentalist Troubleshooting Guide

## Debugging Tips for Loose Filament During Rewinder Operation

After a fast load movement, a full spool may rotate a bit further due to inertia and cause a small amount of filament slack around the spool. This behavior is the same as any roller based spool holder and should not cause any issue for printing. 
*In all other Filamentalist operations, there should be no slack forming on the spool.*
If you observe excessive slack, please read the troubleshooting information below.

### Issue: Slack Forming Around the Spool in the Rewind/Unload Direction

**Causes and Solutions:**
- **Tensioner Settings:** Ensure that the tensioner is not overly loose. It should maintain enough tension so that filament movement drives the rollers.
- **One-way Bearing Direction** Check that the bearing is not installed in reverse. See section 3. Drive Roller Assembly in the main readme.md doc.  
- **Spool Slippage:** If the problem occurs when the spool is nearly empty and the spool is slipping on the roller, make sure you have a high traction material such as rubber bands or bicycle inner tube bands on the rim rollers. 

### Issue: Slack Forming Around the Spool in the Print/Load Direction

**Causes and Solutions:**
- **One-Way Bearing Disengagement:** The issue typically indicates that the one-way bearing is failing to switch to free-wheel mode.
  
  **Assembly Checks:**
  - **Spacing and Alignment:** The one-way bearing should not be tightly sandwiched between the two CDR Spacers and Rim Rollers. Instead, the spacers should have a small allowable movement on the shaft (approximately 0.2mm to 0.5mm) .
  
  **Friction Concerns:**

- **Tight One-Way Bearing:** Verify that the one-way bearing rotates freely on the shaft (has equal to, or leass resistance than a 608 bearing). If one-way bearing feels tight/draggy when rotated on the shaft in the unlocked direction the inner plastic spring/retainer my be too tight.  Ttry reworking the bearing using the procedure below:
  - **One-Way Bearing Rework Procedure** - see video of procedure [here](https://photos.app.goo.gl/rgrtAJLfc5br5F7E9)
      1. Place bearing on end of axle rod/tube.
      2. Heat bearing with heat gun or blow dryer until bearing gets hot.  Rotate bearing while heating to get uniform heating
         - **Since power/heat of heat guns vary it is possible to overheat the bearing and melt the inner plastic!** Check result on the first bearing with every 20-30 seconds of heating by following steps c. and d. below until you determine the correct amount of heating required for your heat gun and tight bearings.
      3. While holding the the heated bearing and axle with a towel or (anything to protect your hands from getting burnt), rotate the bearing on the shaft in the unlocked direction until the bearing cools down.
      4. The bearing should now rotate on the axle with little to no resistance in the unlocked direction but still lock tightly in the opposite direction.  If you still feel excessive resistance (greater than a 608 bearing's resistance), repeat the procedure adding even more heat/time.
  - **Lubrication:** Use a light lubricant (thin layer of lithium grease or silicone lubricant) on the center portion of the shaft where the one-way bearing will sit.
  - **5/16" Diameter Axles:**" As a last resort, purchasing 5/16" diameter shaft or stainless steel tubing should result in an axle diameter less than 8mm

## Gear Motor Stalling

**Causes and Solutions:**
- **Excessive Spring Tension on Tensioner Assembly:**  The tensioner screw may be set too tight not allowing the Tensioner Arm to lift and allow for slip when needed
- **Filament Path Resistance:**
  - Excessive filament path length and bends increases system resistance.  Minimize the filament path length and turns between the Filamentalist and the MMU.
  - Increase bowden ID.  2.5mm ID is the recommended diameter for a baseline setup but 3mm ID may be required for long/high-resistance filament paths.
- **Rubbing/Interference of Filamentalist Components:**
  - Remove the filament from the rewinder and spin the Center Drive Roller assembly and the Rear Idler Roller.  Listen and feel for scraping, rubbing, or excessive resistance. If you feel this then the rewinder may need to be dissassembled and reassembled.  When reassembling check that:
    -  the Rim Roller spacing allows the CDR Spacers to free float
    -  the Rear Idler axle screws are not overly tight and causing lateral compresion on the 608 bearing races
    -  the Rim Rollers are not rubbing against anything
    -  the one-way bearing is free of debris

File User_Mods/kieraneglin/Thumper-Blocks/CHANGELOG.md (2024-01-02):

# Changelog

## Rev 3 (2023-12-15)

All parts except the latch have been modified and are not compatible with previous revisions.

- Beefed up M4 holder to prevent breakage during M4 installation
- Beefed up filament path side walls to prevent breakage during ECAS installation
- Removed 2 layers of width from the filament path to reduce the chance of rub when installed
- Updated base to support roll-in inserts for mounting to the rail
  - Also moved mounting hole just a bit
- Improved magnet fitment on filament path
- Added channel in base to improve filament feeding reliability

**UPDATE (2024-01-01)**

- Added `Thicker` variant to support ERCF v2 spec
- The original `Rev 3` is now in the `Thinner` directory
- The `filament_path` and `base` files are changed and not compatible between variants. The latch and tophat are unchanged.

## Rev 2 (2023-11-10)

- Updated tophat and filament path to use a two-landing design for the `up` vs. `down` positions. This makes the `up` position more reliable and repeatable. Don't forget to use the Springy servo arms!
- Updates some chamfers on the base (inconsequential)

## Rev 1 (2023-08-15)

Initial release!

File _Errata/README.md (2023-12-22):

This folder is for the ERCFv2 dev team.  It contains possible errors and possible updates. Please ignore for now.

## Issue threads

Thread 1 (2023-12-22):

Typo on page 54 of the manual

HitLuca, 2023-12-22:
The manual on page 54 states
> 2x 6x3x2mm Magnets

It should instead be

2x 6x3mm Magnets

MissileLaunchSystem, 2024-01-04:
Resolved by Commit c8028c1 updating the manual. Thanks for the help!

Closed 2024-01-04.

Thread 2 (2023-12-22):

BOM is short on Omron microswitches

GarthSnyder, 2023-12-22:
It looks like one microswitch is needed for each ERCT lane. The master BOM on Google Sheets leaves these out of the count.

Also, the modified toolhead may need two microswitches and two 5.5mm ball bearings if you elect to install both sensors. The spreadsheet only shows one each. I would hate for someone to order from China and discover they're one short three weeks later. 🙂

kinematicdigit, 2024-01-04:
Thanks. The BOM has been updated for this now.

Closed 2024-01-04.

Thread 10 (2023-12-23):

Request to add XOL cutter+sensor

fryc88, 2023-12-23:
Hi,
I know it's only been released, but are there any plans on adding cutter and/or filament sensor to XOLs current build (current build isn't XOL2 by the way):
https://github.com/Armchair-Engineering/Xol-Toolhead/tree/main
My combo is Orbiter2 and Rapido2 uhf, I've looked into some files but my CAD skills are too poor still to get this done on my own :(

fryc88, 2023-12-31:
Anyone? Is it just me who's got that set?

Tyler8299, 2023-12-31:
Ill get with the team to try and work on something. I myself am no good at CAD. I just reviewed the files and noticed the XOL does not support  the X1C hot end.  It's going to take me some time to acquire all this stuff as I run the X1C in all my gear.

fryc88, 2023-12-31:
I would really appreciate it :) no rush with it to, would be just nice to see it at some point

fryc88, 2023-12-31:
> Ill get with the team to try and work on something. I myself am no good at CAD. I just reviewed the files and noticed the XOL does not support the X1C hot end. It's going to take me some time to acquire all this stuff as I run the X1C in all my gear.
Actually there's one for current xol build, however not official, they just shared it on xol discord
https://www.printables.com/model/622854-bambulab-hotend-mount-for-xol_toolhead

Bb06477, 2025-03-07:
https://www.printables.com/model/1214979-g2sa-sensor-adaptation-for-xol2-toolhead

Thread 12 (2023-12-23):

BTT MBB does NOT fit the case.

BlackNet, 2023-12-23:
Checked the upper and lower case.

*) Lower case does fit the screw holes, but it does not fit the board. The lip needs to be wider.

*) Upper case does fit the screw holes; does NOT fit the board due to the components being super close to the screw holes.

BlackNet, 2023-12-23:
Also the cutouts for the cables on the top cover is not wide enough.

BlackNet, 2023-12-23:
the repo was updated with the correct files.

Closed 2023-12-23.

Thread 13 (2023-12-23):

Gneu42 Block End mod issue

Benoitone, 2023-12-23:
@gneu42 I think in your `Filament_Block_End.stl` from your Reinforced Block End Mod the two little conicals holes are missing?
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

gneu42, 2023-12-23:
You are right, they are missing, but I did not remove them.
They were already missing on the part that I used as base for the modification.
They must have been added later on to the V2 final block end.
They are not needed on my setup, since the foot is not under them.
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

Benoitone, 2023-12-23:
> You are right, they are missing, but I did not remove them. They were already missing on the part that I used as base for the modification. They must have been added later on to the V2 final block end. They are not needed on my setup, since the foot is not under them. ![Capture](https://private-user-images.githubusercontent.com/59416685/292635935-21e256e9-7683-48c3-893c-ce83ea8d2da9.JPG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)

Ok. it's the foot from the original SturdyBunny :)

gneu42, 2023-12-24:
I added the 2 missing conicals holes, so it can be use with the official V2 foot.

Closed 2024-01-04.

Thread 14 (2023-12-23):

[FAQ] Could a note be added about V1.1 + Mods -> V2 Compatibility?

ndanyluk, 2023-12-23:
Hi ERCFv2 Team!

Absolutely love the release! I'm already printing parts now :)

Based on a brief discussion on Discord, would it be possible to include a note in the FAQ regarding what can be "carried forward" from V1.1 + the popular mods (Springy, Triple-Decky, Binky, SturdyBunny)?

For example, the written text on a number of the parts bear a strong enough similarity to their mod counterparts that users may mistakenly think they don't need to reprint unless they see obvious changes.

Based on the discussions, the only parts that appear to be 100% carry forward are:

* The parts noted in the build guide as carry forward from V1.1 stock builds
* The Triple-Decky C7.0 filament blocks

Are there any more that fit this description?

ndanyluk, 2023-12-24:
Closing since af0584e367e37f8b150111b897ac7d948c69630b solved my issue :)

Closed 2023-12-24.

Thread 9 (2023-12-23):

Cottontail: [c]_Coupler_Block_180_xN.stl Missing Keyways

GavinHanson, 2023-12-23:
As per title, this file is missing the Male + Female keyways to lock it into the main body.

D20180, 2023-12-26:
ERCF_v2/tree/master/Recommended_Options/ERCT_Buffer/Options/180_Degree_Build/Coupler_Block)
/[a]_Coupler_Block_180_xN.stl

Missing support for led holder opening.

MissileLaunchSystem, 2024-01-04:
This was fixed in commit a1aded5. Thanks you for helping us improve!

Closed 2024-01-04.

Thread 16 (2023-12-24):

[Easy BRD] Missing Support Material

tinyfluffs, 2023-12-24:
`[a]_ERCF_Easy_Brd_Bracket_Bottom.stl`

Part is missing the built-in support material in the repo

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

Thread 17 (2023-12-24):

Typo page 81

D20180, 2023-12-24:
Piece of filament labeled "M" should be "P"

MissileLaunchSystem, 2024-01-04:
Resolved by Commit c8028c1 updating the manual. Thanks for the help!

Closed 2024-01-04.

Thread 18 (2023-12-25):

Missing [a]_Support_Arm_Mount_xN.stl

mszulen, 2023-12-25:
Instead, there's [a]_Support_Arm_xN.stl duplicated as [a]_Support_Arm_Mount_xN.stl

mszulen, 2023-12-25:
Ok, just noticed that this has been fixed just after I downloaded the repo.
Closing....

Closed 2023-12-25.

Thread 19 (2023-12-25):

[a]_Support_Arm_xN.stl rabbit placed 1 layer above the bed

mszulen, 2023-12-25:
Is this intentional? There's a single layer space between beed and the rabbit figure in the Support Arm file.

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

o1hitman1o, 2023-12-26:
@mszulen How are you getting bridging on the first layer. I can't see to get it only on the second layer and when I try to print it wants to fail.

mszulen, 2023-12-26:
It does print but it's not looking good as you can see.
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

o1hitman1o, 2023-12-26:
It does appear that maybe this was a mistake, other photos on discord show it being solid on the first layer...
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

mszulen, 2023-12-26:
then the file in STL folder is wrong/broken.

o1hitman1o, 2023-12-26:
Per Terrance on Discord it is supposed to be one layer higher to give a texture to the rabbit.

mszulen, 2023-12-26:
oh.. ok. Anyway... it won't be visible once assembled :) Not a big issue :D

o1hitman1o, 2023-12-26:
I guess the issue can be closed then.

Closed 2023-12-26.

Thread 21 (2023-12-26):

2020 mounting parts

Anollya, 2023-12-26:
Please make cuts in the 2020 mounting parts for the T-Nuts.
The parts dont hold in the 2020 extrusion.

wrong
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

ok:
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

affected parts:
Stls/Filament_Blocks/End_Bypass.stl
Stls/Gear_Box/Gear_Box_Front.stl
Stls/Filament_Blocks/[a]_End_Bypass_Foot.stl

Tyler8299, 2023-12-26:
You are using T slot 2020 and not V slot 2020 correct? Are you using Drop in nuts/Hammer T nuts or spin in nuts? Hammer T nuts are almost form fitting giving no locking force please try drop in nuts

Tyler8299, 2023-12-26:
[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]()

Tyler8299, 2023-12-26:
Here is an example of how both nuts engage the extrusion and if using V slot will compound the problem even worse 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

Tyler8299, 2023-12-26:
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

ZeraLes, 2023-12-26:
Thank you Tyler, I. Using only the the ones for drop in with a spring lick and steel ball. I'm coming from the mechanic sides. And yes only t nut not vslot. Having my problems collecting 4050 double t nut here in Germany for my EZBake trident Projekt for 24/25 😬. Thanks a lot for the info, already ordered a 2020 on my fav shop here. Regards Boris --Diese Nachricht wurde von meinem Android Mobiltelefon mit WEB.DE Mail gesendet.Am 26.12.23, 16:23 schrieb Tyler ***@***.***>:

  You are using T slot 2020 and not V slot 2020 correct? Are you using Drop in nuts/Hammer T nuts or spin in nuts? Hammer T nuts are almost form fitting giving no locking force please try drop in nuts
  —Reply to this email directly, view it on GitHub, or unsubscribe.You are receiving this because you are subscribed to this thread.Message ID: ***@***.***>

Anollya, 2023-12-26:
Hello Tyler,
thank you for your fast response.
I´m using V-Slots. I tested drop in nuts as well, the same.

i measured it:

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

V-Slot ~1,4mm - 0,7mm (drop in nut) = 0,7mm -> the part has 1,1mm -> 0,4mm to much.
i dont know, may be i bought the 2020 from a wrong dealer.

tinyfluffs, 2023-12-26:
I do personally second this change. Having the option to use hammer heads or roll in nuts would be greatly appreciated.

arkeet, 2023-12-30:
I noticed this too when trying to assemble with cheap slide-in nuts with a 1.2mm step (but with Misumi T-slot). I think 1.1mm on the part is excessive - for reference, I checked some similar features on a few Trident parts, and they have just 0.6-0.7mm extending into the slot, so I think that is sufficient.

The filament blocks have a cutout so they don't have this issue.

WizardUli, 2024-04-04:
I have this profile https://www.vsk-profily.cz/hlinikovy-profil-bh-20-6-20x20/ with spare nuts from LDO Voron kit and it's completely unusable. Gearbox and filament blocks are still completely loose after tightening them.

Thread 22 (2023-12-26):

Filament cutter- main body cw2 issue

bartoszwas, 2023-12-26:
Hey all,

CW2 main body for filametrix is missing a piece where cable/board cover goes. Marked on picture below.

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

Tyler8299, 2023-12-27:
This is to allow access to the thermistor connection on the bTT ebb 2209 so you do not have to disassemble more than needed

ambethia, 2024-02-22:
This is not even really where the thermistor plugs in, it's further down, off the PCB.

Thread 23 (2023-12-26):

CottonTail buffer - slicing issue.

bartoszwas, 2023-12-26:
Hey all,

In CottonTail buffer is hard to print that rabbit in the middle 'cause it starts on second layer...
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

o1hitman1o, 2023-12-26:
According to Terrance on discord it is meant to be that way to add texture. He suggested you can also just [add this rabbit](https://cdn.discordapp.com/attachments/1165841694273585234/1189292318038184016/a_Support_Arm_Mount_Bunny_xN.stl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) in
with this part, and make it flush to the plate. I just edited the STEP file to pull it to the surface so mine prints correctly. Attached are the files is used.
[Support_Arm.zip](https://github.com/Enraged-Rabbit-Community/ERCF_v2/files/13773998/Support_Arm.zip)

o1hitman1o, 2023-12-26:
I feel this should be made as a 2 part object instead of a reces. That way if you wanted to print this as multicolor you could.

bartoszwas, 2023-12-26:
Yeah, multicolor would be a good option. Better then printing that complicated model in mid air...

w35t13, 2023-12-28:
if it was designed abit better maybe it could work but how it is just makes the hole rabbit print midair.

o1hitman1o, 2023-12-30:
@bartoszwas Looks like and updated support arm was added so it easier to print. If this works I think this issue could be closed.

Closed 2024-01-02.

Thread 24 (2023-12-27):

Documentation issue on page about Wiring the MMB

jaketri, 2023-12-27:
The manual page about Wiring the MMB (page 125 on current version of the documentation PDF) have pre-gate sensors using MMB connectors STP1 - STP8 and also shows jumpers ON for DIAG1 and DIAG2 (gear and selector motors). Based on [MMB documentation.](https://github.com/bigtreetech/MMB/tree/master/Hardware) STP1 / STP2 and DIAG1 / DIAG2 share same GPIOs (PA3 / PA4). Also the STP9 and STP10 are not used so a quick fix is to shift the pre-gate sensors to use STP3 - STP10 and reserve PA3 and PA4 GPIOs (used by STP1 and STP2) for DIAG1/2 signals.

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

o1hitman1o, 2023-12-29:
This seems correct but also their might be something wrong with MBB documentation. I see that STP3(STOP-3) connects to pin PB8 but  STP4(STOP-4) connects to pin (PB7) but on the Schematic is shows from the MCU section PB9 is STOP-3 and PB8 is STOP-4, PB7 is M4-DIR.
Upon further research It seems this is an issue in the documentation on MMB [Link](https://github.com/bigtreetech/MMB/issues/7)
Overall I think you are correct with this (if you plan on using sensorless homing for any of the motors), you will need to leave STP1 & STP2 open. If not then you would not use the jumper pin on DIAG1 or DIAG2 and can use STP1&2 for the pre-gate sensors.

o1hitman1o, 2024-01-02:
@jaketri  looks like this was just updated. Close issue?

jaketri, 2024-01-02:
Closing issue as fixed by latest documentation update

Closed 2024-01-02.

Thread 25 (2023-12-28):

Manual: calibration tool instructions

shiftingtech, 2023-12-28:
on page 4, the manual states

"Beware that this project requires a well tuned printer and slicing profile, as there are many press fits and plastic on plastic
mechanisms. You should first print the ERCF_Calibration_Tool.stl, test the part, as shown in the manual, tune your printer and
profile if needed, and then only print the rest of the parts"

This should mention that you actually need to print TWO parts:  one of the tests appears to be a fit test between the calibration tool, and the tophat.

(easy enough to figure out a few pages later, but I for one had already hit print before I got to the page saying how to read the thing...)

MissileLaunchSystem, 2024-01-04:
Resolved by Commit c8028c1 updating the manual. Thanks for the help!

Closed 2024-01-04.

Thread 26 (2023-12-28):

Manual: additional tools note

shiftingtech, 2023-12-28:
Page 8 states

"ADDITIONAL TOOLS
We provide additional tool recommendations in
our sourcing guide. Visit https://vorondesign.com/
sourcing_guide and switch to the “Voron Tools”
tab at the bottom of the page"

This is a potential source of confusion, since ERCF has it's own sourcing guide/BOM.  I would suggest phrasing it as something like:

"ADDITIONAL TOOLS
The tools needed are similar to those used building a
Voron. For recommendations, visit https://vorondesign.com/
sourcing_guide and switch to the “Voron Tools”
tab at the bottom of the page

MissileLaunchSystem, 2024-01-04:
Resolved by Commit c8028c1 updating the manual. Thanks for the help!

Closed 2024-01-04.

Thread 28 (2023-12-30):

Screws attaching parts to 2020 extrusion dig into the bottom of the slot

arkeet, 2023-12-30:
The parts are modelled in such a way that the M3x8 screws extend 6.1mm into the slot (see first picture below), which is larger than the 6mm depth of the slot. In addition, due to compression of the part, as well as the possibility of a screw being over nominal length, the actual distance the screw goes into the slot can be even greater. In my designs I try to leave at least 1mm of space between the screw and the slot bottom (i.e. screw should extend 5mm into the slot, which means a distance from counterbore to the face that touches the surface of the extrusion should be at least 3mm for a M3x8 screw) to avoid this. A quick survey of Trident and V2 parts shows a range of 1.0-1.6mm for screw to slot bottom distance.

Affected parts (locations circled in red below):
* Gear_Box_Front (4 screws)
* End Bypass (1 screw)

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

MissileLaunchSystem, 2024-03-13:
I just merged these changes. Thanks for the help!

Closed 2024-03-13.

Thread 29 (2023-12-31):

[Documentation] Missing instructions for Easy BRD install, and other boards

tinyfluffs, 2023-12-31:
Had to figure this out for myself. There's no CAD for Easy BRD either, so it wasn't immediately obvious where and how to mount the board. Would be good if there was a document on the Git repo at the very least, but ideally incorporated into the manual.

spikeygg, 2023-12-31:
This is a duplicate of https://github.com/Enraged-Rabbit-Community/ERCF_v2/issues/16

tinyfluffs, 2024-01-01:
> This is a duplicate of #16

That's my own. And no, it's not a duplicate.

sharpner, 2024-01-30:
@tinyfluffs could you share how you did it? I am currently stumbling over this as well^^"

tinyfluffs, 2024-01-30:
> @tinyfluffs could you share how you did it? I am currently stumbling over this as well^^"

Sure! Here's some photos from my build log. Basically, two t-nuts for the mounting frame. Then it's M3 screws threaded into plastic for the MCU.

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

sharpner, 2024-01-31:
awesome thanks so much - looks super clean :)

tinyfluffs, 2024-02-01:
> awesome thanks so much - looks super clean :)

No problem! One thing I do recommend is running a separate 5V rail to your servo. The Easy Brd 5v rail is not powerful enough to handle ERCFv2, as it needs extra current. If you have a 5V PSU you can just run the single cable from there, provided the grounds are tied together with the 24V.

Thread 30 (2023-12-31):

BOM wrong for 5.5 Ball

Mac2712, 2023-12-31:
BOM shows 5.5mm Ball for CW2 main body for filametrix looks like a 7mm ball is needed for the bearing switch.

o1hitman1o, 2024-01-02:
I agree with this. BOM says 5.5 but Filiametrix says 7mm.

bartoszwas, 2024-01-02:
Yeah that filamterix is a mess, every variant is different and propably cable cover won't fit either...

Mac2712, 2024-01-02:
I purchased some ball's just for this because it was on the BOM in the end I printed a ball shaped spacer that works nice

kinematicdigit, 2024-01-04:
We are investigating this further, and yes, some of the mods have 7mm balls. We are trying to make them all standardized to 5.5 balls. Apologies for that. We are going to address this as soon as possible and will post updates. In the meantime, if you can find 7mm balls, use them, but we will be moving forward with one standard.

kinematicdigit, 2024-01-04:
> Yeah that filamterix is a mess, every variant is different and propably cable cover won't fit either...

We did try to ensure the covers and latches all match. We will double check those as well.

EmJay276, 2024-01-17:
@kinematicdigit let me know if you need any changes in these parts here
https://github.com/Enraged-Rabbit-Community/ERCF_v2/pull/7

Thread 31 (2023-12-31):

Add end without bypass

juliusjj25, 2023-12-31:
I am able to retain my 6 lane setup from V1.1 without the bypass and I am sure others are as well. It would be nice for this to be included, however it can be done in the slicer fairly easily as well by adding negative volumes, however it removes the second set of screws to hold it to the extrusion.
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

moggieuk, 2024-01-09:
We debated support for this a lot.  One of the goals was to have a "standard" CAD layout to make setup and automation easy.  This changes those assumptions.  You should, of course be able to do it, but I think it best served as a user modification that includes with it details on what to change in the Happy Hare config to support.  Some of the advanced `cad_` parameters need to be determined and tweaked:
E.g.
```
#cad_bypass_offset: 0			# Distance from limit of travel back to the bypass (ERCF v2.0)
#cad_last_gate_offset: 2.0		# Distance from limit of travel back to last gate
#cad_selector_tolerance: 10.0 		# How much extra selector movement to allow
```

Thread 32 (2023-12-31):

New easier to print [a]_BTT_MMB_Support_Arm_Endcap_Bunny_Outline.stl does not have cutouts for alignment with coupler blocks.

Ekodas, 2023-12-31:
The new easier to print [a]_BTT_MMB_Support_Arm_Endcap_Bunny_Outline.stl does not have the 3 alignment cutouts to allow it to mate with the coupler blocks.  The old version did have these cutouts.

Also, the hole for attaching to the last [a]_Support_Arm_Mount_xN doesn't line up either.

o1hitman1o, 2024-01-02:
- [ ]
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
This is confirmed. Need to update easy to print version.

MissileLaunchSystem, 2024-01-04:
Resolved with a commit I just pushed a minute ago. The new file is available here:
Recommended_Options/ERCT_Buffer/Stls/Support_Arm/Bunny Logo Outline (easier to print)/[a]_BTT_MMB_Support_Arm_Endcap_Bunny_Outline.stl

theminjus, 2024-01-06:
i would reopen this one ,
[a]_Support_Arm_Endcap_No_Electronic_Box_Bunny_Outline.stl
is hole is not aligned for the endcap heat insert

Closed 2024-01-04.

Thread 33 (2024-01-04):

Fushibering wants to participate in the testing and verification of accessories

fushibearing, 2024-01-04:
Dear friend, hello,
I saw the introduction, Manufacturers: If you want to be included, please contact us. We are happy to validate your kit/parts and then add you to the list
I am William, a sales engineer at FUSHI Bearing,
And I really want to participate in this validation.

We can provide high-quality bearing sets.
We have nearly 30 years of production experience in bearings,
Then we also developed some special bearings for 3D printers this year,
As shown in the LM8uu black chrome bearing below, the quietness and operating efficiency are 25% higher than RJ4JP-01-08.

We are willing to provide high-quality and cost-effective bearing sets for the community.
And we have experience collaborating with Prusa and other 3D brands.
Bearings play an important role in the energy efficiency ratio of transmission,
We are confident that we can provide better bearings according to your needs.
Improve the accuracy and stability of the printer.
If you are interested, please contact my email: williamliu@fushibearing.com
Thanks

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

Closed 2024-01-17.

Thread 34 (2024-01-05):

The Toolhead Sensor-only EBB CW2 Body STL should be paired with EBB Cable Cover

jfgordon2, 2024-01-05:
The [SB_CW2_Body_EBB.stl](https://github.com/Enraged-Rabbit-Community/ERCF_v2/blob/master/Recommended_Options/ERF_Filament_Cutter/Stls/2_Toolhead_Sensor/SB_CW2_Body_EBB.stl) does not fit the standard cable cover.   As this is a nice option for a lot of stealthburner PCBs, it might make the most sense to just provide a link to or a copy of the [BTT cable cover for EBB](https://github.com/bigtreetech/EBB/blob/master/EBB%20SB2240_2209%20CAN/STL/Cable_Cover_For_PCB_V1.1.STL) in this repo that fits this specific design.

This is an issue as users may casually decide to just go with a single sensor, and it is not obvious if you aren't initiated on what "EBB" might refer to that you need an alternative cable cover to fit this design.

ambethia, 2024-02-22:
Same issue here.

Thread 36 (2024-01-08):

Cottontail- Doc/CAD Improvement - Clear Parts

Max-Luck, 2024-01-08:
Hi!

Would it be possible to change the colors of the parts represented in the CAD and documentation for the Cottontail clear parts?

In the cad / documentation currently:
[c]_Coupler_Block_xN.stl is rendered in accent colors
[a]_LED_Carrier_xN.stl is rendered in an off color interpreted to be the clear part

I think if you flipped the color of the parts, it would greatly improve the understandability of the documentation and CAD.

Thanks!

Example:
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

Maybe something like this would be better?
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

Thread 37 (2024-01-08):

Documentation: order of operations for gear box assembly

GarthSnyder, 2024-01-08:
I've had a really good experience with the docs so far. What a huge amount of work must have gone into this!

However, one thing has tripped me up not once but twice, in both cases costing 20 minutes or more of backtracking. It's probably an issue inherited from V1 of the ERCF manual, but the fact that a lot of people will be upgrading from V1 likely makes it worse.

Page 45 helpfully advises, "Make sure the wires are routed in the channel between the 2020 extrusion and the Gear_Box_Back. If you route the wires through the other opening, you won’t be able to connect the wires later!"

The problem is that by the time you reach this instruction, the pass-through area has already been fully locked down. Unfortunately, it isn't large enough to accommodate any sort of connector, even a JST. If your cables have connectors on them, you have to de-construct all the way back to page 34. In particular, you have to release the set screws on the 20T pulley and remove the gear wheel from the D shaft, because there are screws that hold earlier parts together that can't be accessed through the gaps in the wheel.

As I said, I blundered into this problem twice. The second time, I was actively thinking "make sure to keep the cables routed properly so you don't run into that same problem again!" I had forgotten the details, though. The fact that several parts have cutouts for cables lulled me into a false sense of security. The actual pass-through is small, asymmetrical, and half lined with sharp-edged 2020 extrusion, so it doesn't really announce itself as the designated route.

It would be helpful to have a note at the top of page 34 that says something like, "Installing the Gear_Box_Back will finalize the path out of the gear box for ALL wiring in this half of the ERCF, including the wiring for the endstop switch, the gear motor, and any wiring that emerges from MicroFit connectors (if you use them). You can thread wires through the gap later, but there isn't enough room for crimped-on connectors. If your wiring is pre-crimped (e.g., if you are upgrading from ERCF V1), make sure that ALL wiring goes through the cable channel NOW. If you do end up with a straggler cable, it's likely more time-efficient to cut off one end and recrimp than to disassemble the gear box."

MissileLaunchSystem, 2024-03-13:
I merged in Ark's fixes that add more wiring clearance to the gearbox to help address this. This is as fixed as this issue will get until we redesign the gearbox.

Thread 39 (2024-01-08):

Thumper README: encoder_parking_distance is now called gate_parking_distance

GarthSnyder, 2024-01-08:
I think... Not sure of the exact history here.

MissileLaunchSystem, 2024-03-14:
Did Kieran fix this? It's an issue for him - while we do work with Kieran, Thumper Blocks are not a first-party ERCF component at this time, so do [https://github.com/kieraneglin/Thumper-Blocks](let him know) if this is still an issue.

Tyler8299, 2024-03-14:
I believe this is just the Evolution of Happy Hare and letting users of his blocks know the change software change

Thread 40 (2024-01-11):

Add Encoder push tool to the STL's as is missing

PaulMellor, 2024-01-11:
Had to go looking for the encoder tool, can we please add it to the Tools or the encoder section of the STL's

https://github.com/mneuhaus/EnragedRabbitProject/blob/e0272b7838a99c0ad8416ad5d3ec9c45b1973cac/usermods/Binky/STL/Tool_Encoder_SlottedWheel_PushTool.stl

Benoitone, 2024-01-11:
it's on the [Tools folder](https://github.com/Enraged-Rabbit-Community/ERCF_v2/blob/master/Stls/Tools/Slotted_Wheel_Push_Tool.stl).

Closed 2024-01-12.

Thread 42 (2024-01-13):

[ERCT] Front tag plate slot has the notch in the wrong location

arkeet, 2024-01-13:
This is a trivial issue but I am reporting it anyway.

Please see the picture. The notch just needs to be moved 7.5mm to the right.

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

arkeet, 2024-01-18:
I think 7.5 is correct, the tag plate intersects the arm in CAD if that's what you were using as a reference. Not that 0.05mm would matter when printed.

arkeet, 2024-01-19:
Yes, the missing 0.05mm is because of the 0.05mm overlap in the model 🙂
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

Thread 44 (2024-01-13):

STL and BOM duplicate and misnamed files

gitgotgit, 2024-01-13:
These files can be found in 2 locations on GitHub, and the BOM consequently lists them twice even though only one copy is required:
[a]_BTT_MMB_Box_Lid.stl
[a]_BTT_MMB_support_arm_bottom.stl

Located in:
ERCF_v2 / STLs / Supports / BTT_MMB / Buffermount_for_ERCT
and also in:
ERCF_v2 / Recommended_Options / ERCT_Buffer / Stls / Support Arm

In addition "[a]_BTT_MMB_Box_Lid.stl" is incorrectly called "[a]_BTT_MMB_case_top.stl" in the BOM

MissileLaunchSystem, 2024-03-13:
Issue 1:
They are indeed duplicated. I think it is a remnant from reorganizing folders, I will double check with the team before deleting.

Issue 2:
You're referring to the Printed Parts Tracker, not the BOM, correct? I've fixed the filenames for a few things in the Tracker.

Issue 3:
There is a method to print the tag plates on a single-color printer with manual color changes so that you can print them before setting up ERCF. I'll ask the team to find that info and add it to the manual.
I do not believe the color inversion was deliberate, I will ask the team.

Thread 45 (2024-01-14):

Apron LEDs

Zephyrus67, 2024-01-14:
Does the apron leds do anything besides throwing light inside the Voron printer through the top panel?

moggieuk, 2024-01-19:
Yes!  There are certain effects that occur for operations but the functional part is that they can show the filament color or gate_state .. gate have filament or not as well as indicate error conditions and filament swaps.  It certainly isn't necessary but a nice feature and more than just lights.  Here is an example through the HH command:
```
> MMU_LED
LEDs are enabled
Default exit effect: 'gate_status'
Default entry effect: Unavailable
Default status effect: 'filament_color'

Options:
ENABLE=[0|1]
EXIT_EFFECT=[off|gate_status|filament_color]
ENTRY_EFFECT=[off|gate_status|filament_color]
STATUS_EFFECT=[off|on|filament_color]
```

Zephyrus67, 2024-01-19:
Thank you very much. I already have case lighting so I would not use the aprons if all they did was throwing light into the case. But in this case as you describe I will print out the aprons as well.

I am not 100 % certain yet where I will place the ERCF (might go on the back of the printer) so I might make a new standalone panel for the aprons instead but I will see that later.

Closed 2024-01-21.

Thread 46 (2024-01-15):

Toolhead Sensor Part Mismatch

tinyfluffs, 2024-01-15:
The 2x sensor options, with and without filametrix, differ drastically at the top gear sensor. There is no hole to visibly see the position of the ball bearing, and it makes it impossible to know whether it is engaging beyond a very faint click (I'm hard of hearing).

Would appreciate if the two options would match. I had previously installed Filametrix, but I am removing it.

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

Max-Luck, 2024-01-15:
Messaged you on Discord in ERCF_Questions in the Voron Discord

Here is the file just in case
[Stealthburner_CW2_Filament_Sensor_ECAS_tinyfluffs.zip](https://github.com/Enraged-Rabbit-Community/ERCF_v2/files/13943519/Stealthburner_CW2_Filament_Sensor_ECAS_tinyfluffs.zip)

Let me know if this works for you and I can make a pull request

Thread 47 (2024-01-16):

ERCFv2 Manual: page 99 inconsistent screw specified

akempster, 2024-01-16:
Git hash: 7f9bdc8b411cc4deb2719941ea4e03b8cd38f689

What i observed
For the encoder assembly on page 99 the diagram specifies an M3x8 BHCS when the assembly text below indicates M3x8 SHCS.

What i think it should do
Either diagram or text should be updated to the correct option or the text should be updated to indicate either screw type may be used.

recrudesce, 2024-01-16:
I don't think it matters, all it does is actuate the endstop.

Closed 2024-03-13.

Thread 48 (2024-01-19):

[Toolhead Sensors] Add Kapton tape to BOM

tinyfluffs, 2024-01-19:
There's a very narrow clearance between the toolhead sensor microswitches and an SB2040v2. Other toolhead PCBs are probably affected by this too.

To prevent shorting, I recommend we add a piece of kapton tape to the BOM, so people can opt to add it behind the toolhead PCB, should it be required.

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

Tyler8299, 2024-03-09:
This is up to the user to decide as there are too many different boards available. I personally have not had any clearance issues using CW2 or G2E but i also use the ebb2209.

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

Closed 2024-03-13.

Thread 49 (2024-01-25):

ERCFv2 Manual: Page 40, Motor Arm Microfit specified for local MCU (Should be for remote)

iwm911, 2024-01-25:
Hi,

in the manual the text specifies to use the Microfit motor mount for the local MCU setup, which is wrong by the text on page 44.
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

which one is the right one?

MissileLaunchSystem, 2024-03-13:
Apologies for the confusion, the microfits are for use with a remote MCU. I have fixed this in the live manual file and it will be reflected the next time I push a new manual PDF. Thanks for catching that!

Closed 2024-03-13.

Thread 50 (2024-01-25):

ERCFv2 Manual: No reference for 2 part Tophats screws

iwm911, 2024-01-25:
Hi,

there is no reference in the manual (that i could find) to the 2 parts top hats, how to assemble them and so on.

benthetechguy, 2025-02-14:
Any updates on this? Am I supposed to glue them together?

hreality, 2025-03-30:
Old thread.. also printed these and a search led me here first.  So, for the next guy I will say "For me M2x10 self tapping" is what I used without issue.

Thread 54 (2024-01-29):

ERCF Manual: Cotton tail Arms wrong screws

DianosOdd, 2024-01-29:
The manual at page 133 indicates M3X16 screws to connect support arm and mount while M3X20 are necessary

Closed 2024-01-29.

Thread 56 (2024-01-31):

gearbox microswitch wiring local mmu

sharpner, 2024-01-31:
hi guys,

i am building my ercf using a local mmu and therefore skipped from page 18 to page 21, and so on. "Skip to page 21 if you’re using a local MCU."

Then continued with the manual and build the whole thing without ever attaching wires to the microswitch.

Of course that was dumb, and maybe I overlooked something, but since every other step is explained in such fine detail, I think it would be important to also show where the microswitch cables go, or at least a short sentence that we should not forget it at page 28 would be awesome :D

Closed 2024-03-13.

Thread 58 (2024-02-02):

PartsTracker incorrect printed count

mikeytdisco, 2024-02-02:
The printed count cell O263 doesn't cover the whole range of parts.

MissileLaunchSystem, 2024-02-03:
Fixed. Thank you for your contributions.

Closed 2024-02-03.

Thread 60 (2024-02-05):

G2E Toolhead and Entry Sensor STL on 2_Toolhead_Sensor

gralves2, 2024-02-05:
The files SB_G2E_Front_Body_EBB.stl and SB_G2E_Rear_Body_EBB.stl contain both Toolhead and Entry sensors, but they are located on the folder Recommended_Options\ERF_Filament_Cutter\Stls\2_Toolhead_Sensor. Shouldn`t they be on Recommended_Options\ERF_Filament_Cutter\Stls\1_Toolhead_And_Entry_Sensors ?

IRTrail, 2024-02-07:
I am working with the ERCF team to resolve some of these issues. I have a PR in as we speak.

Thanks for the heads up.

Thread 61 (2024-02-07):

Integrated support is not printed correctly

mboo83, 2024-02-07:
The support is only partially printed. Different slicers and settings show the same result.

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

alexstone, 2024-02-08:
I printed with Arachne wall generator and managed to get the support to print. However, without this setting, those supports straight up _do not_ print and you end up with blocks you can't really use.

I would prefer to see the block without the in-build supports, and markers in the docs of where to add them. This would allow the use of interface materials for cleaner bottom surfaces.

mboo83, 2024-02-09:
Thank you, i will give it a Try. You can export it from the CAD Version with Fusion 360 and remove the Support. I printed the one that comes with the Thumper Blocks Mod. That did came out perfect with the integrated Support.

MissileLaunchSystem, 2024-03-13:
I've added support-less versions of the Filament_Path, Tophat, and Base under the sub-folder "No_Supports."

Closed 2024-03-13.

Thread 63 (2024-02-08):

request for a file to put a list of parts

StalkFPV, 2024-02-08:
english:

and they should have a read me with the list of materials needed for the Project and also the number of pieces to print example for 4.

because I am French and frankly I have the complete file and I am totally lost because I don't even know which part exactly goes where and the number of parts to print.

so it would be great if the creator or someone from the community helps people who are lost or new

anyway great job

french :

et ils faudrait avoir un lisez moi avec la liste de matériel qui faut pour le Project et aussi le nombre de pièce a imprimer exemple pour 4 .

car moi je suis français et franchement j'ai dl le dossier complet et je suis totalement perdu car je c'est même pas quel pièce exactement qui va ou et le nombre de pièce a imprimer .

du coup cela serrait le top que le créateur ou une personne de la communauté aide les personne qui sont perdu ou nouvelle

en tout cas super boulots

olivbd, 2024-02-08:
The "list of materials" is called "BOM" - Bill Of Material. You can find it on the [README.md](https://github.com/Enraged-Rabbit-Community/ERCF_v2/blob/master/README.md) file of this project

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

StalkFPV, 2024-02-08:
thank you, I hadn't even seen it. then we cannot modify the number of blocks, but I made a request.

olivbd, 2024-02-08:
> thank you, I hadn't even seen it. then we cannot modify the number of blocks, but I made a request.

When you open this spreasheet, it's in read-only mode. You have to make a copy (File -> Make a copy) and then you will able to modify the number of filament blocks.

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

StalkFPV, 2024-02-08:
thank you damn really google drive is really not my strong point

olivbd, 2024-02-08:
You're welcome.

Could you close this issue?

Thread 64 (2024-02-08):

Suggest adding more clearance to the gear box to route motor wires through

alexstone, 2024-02-08:
I wanted to replace my NEMA14 with a NEMA17. When trying to remove the NEMA14, I found that I actually had to disassemble the _entire_ ERCF to get the cable out without snipping it and re-doing the housing. An extra few millimeters here would really help with maintenance.

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

mboo83, 2024-02-09:
I did the same Mistake. You can easyly pinout the Cables and pull them through the Hole.

MissileLaunchSystem, 2024-03-13:
I've merged Ark's changes that add more space to the wiring path. This is as fixed as it is going to get until we redesign the gearbox.

Closed 2024-03-13.

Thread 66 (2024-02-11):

[documentation] selector assembly steps

shiftingtech, 2024-02-11:
There are a few abnormalities around the assembly of the selector mechanism:  nothing difficult to figure out, but they stand out after the earlier part of the manual

Page 106: calls for 2x M3x12mm SHCS and 1x M5x30mm BHCS which are in the exploded view, but aren't actually shown getting used until later

I think the M3x12 *could* be shown going in on page 108.  They currently don't go in until page 111, which also works, but if they aren't going in until there, I'd suggest not listing them on page 106

the M5x30 doesn't actually seem to be required in this part of the manual at all.  It's called out again on page 116, which seems fine to me.  (I think, similarly, the other one is also called out twice:  page 74, and page 116)

Why am I noticing such nitpicky things, you ask?
Well, my assembly process was, each time I hit an exploded view, I'd locate all the parts it lists, and lay them out on my table.  Then I'd follow the assembly steps until my table was empty again.  If I had parts left over, I knew I'd missed something.  This worked very well, right up until page 108, then it got a little weird.

MissileLaunchSystem, 2024-03-13:
I've added footnotes to the manual that call out how the parts are shown for completeness and not used until Final Assembly. Most of the images are going to need to be redone for the gearbox redesign which is some months out, so we will fully rearrange these pieces then.

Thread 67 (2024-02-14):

ERCT Overhanging Rabbit

3DPrintDemon, 2024-02-14:
The rabbit logo on file [a]_BTT_MMB_Support_Arm_Endcap.stl is an overhanging surface of 0.25mm off of the build plate, Orca/Prusa slicers will not support it.
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

o1hitman1o, 2024-02-14:
@3DPrintDemon it's is definitely and issue and it would work if the slicer realized it was unsupported and bridge printed it but the slicers I have used wants to print the outline of the shape first and the edges at the curves want to print in mid air.
This is the solution though.
https://github.com/Enraged-Rabbit-Community/ERCF_v2/tree/master/Recommended_Options/ERCT_Buffer/Stls/Support_Arm/Bunny%20Logo%20Outline%20(easier%20to%20print)

3DPrintDemon, 2024-02-14:
> @3DPrintDemon it's is definitely an issue and it would work if the slicer realized it was unsupported and bridge printed it but the slicers I have used wants to print the outline of the shape first and the edges at the curves want to print in mid air.
> This is the solution though.
> https://github.com/Enraged-Rabbit-Community/ERCF_v2/tree/master/Recommended_Options/ERCT_Buffer/Stls/Support_Arm/Bunny%20Logo%20Outline%20(easier%20to%20print)

Hi. Yes it needs an outline on layer 1 then it would be able print the rabbit as an unsupported bridge, however as you say the outline starts on layer 2 with nothing under it so it prints in mid-air.

Indeed, I mentioned about those outline files, it would be good to include them with the files at the link I posted above along with the main ERCF files, as it is they’re only available deep in the folders of the ERCT files, not that obvious to people unfamiliar with the directory structure & find only the regular ones in the ERCF folder first.

Tbh it would probably be best to take the regular files down or fix them as Orca & Prusa simply won’t print them correctly.

wagnerism, 2025-03-09:
This is causing failed prints in both PrusaSlicer and OrcaSlicer.  The first one or two worked. I had several failures until I looked at the second layer.  There should be an outline of the rabbit on the very first layer.

This is a poorly-implemented and unnecessary cosmetic feature.

STL uploads are not allowed here so I filled in that first 0.25mm layer and uploaded it here.  https://github.com/wagnerism/tamed_rabbit/blob/main/%5Ba%5D_Support_Arm_tamed_rabbit_of_death_xN.stl

Here's the first layer:

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

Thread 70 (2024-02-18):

Apron LED Documentation

eprouty, 2024-02-18:
On page 22 of the ECRFv2 Manual it shows instructions for wiring the apron LEDs, but then there are no instructions for installing them, is this an oversight or are those instructions elsewhere in the documentation?

MissileLaunchSystem, 2024-03-13:
It is an oversight - most of the dev team didn't have LEDs to play with when we did the last major push to get to release. More of us have LEDs now, so we're going to try to add that soon.

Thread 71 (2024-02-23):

Toolhead Sensor only for ERF wrong STL

eprouty, 2024-02-23:
https://github.com/Enraged-Rabbit-Community/ERCF_v2/blob/master/Recommended_Options/ERF_Filament_Cutter/Stls/2_Toolhead_Sensor/SB_CW2_Body_EBB.stl

This piece does not properly trigger the sensor:
1. It has a hole to fit a 7mm ball, not the 5.5mm that is used by option 1
2. The cutout for the switch is slightly too small
3. The ball never makes contact with the switch when inserting filament.

billgeek, 2024-05-05:
I know this is old, but I ended up "solving" this by cutting and reinstalling the switch lever. I know it's not a great solution, but it works for now.

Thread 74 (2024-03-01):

Match Selector Parts for Matched Material Shrinkage

Tuckpolo, 2024-03-01:
Ideally you have your filament dialed in, but to improve build Selector Cart, Linear Axis Idler Block, and Linear Axis Selector Motor Support  should all be made from the same material. I would propose changing them all to the accent color.

MissileLaunchSystem, 2024-03-13:
If your ABS is inconsistently shrinking between colors, you need better ABS. This has been debated extensively on Discord, so apologies for the short answer.

Closed 2024-03-13.

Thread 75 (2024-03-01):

Additional View for End Stop Wiring

Tuckpolo, 2024-03-01:
Add a view similar to PG 44 but for the endstop at page 34, or 30 demonstrating the wire connecting to the correct pins and routing out the bottom.

Closed 2024-03-13.

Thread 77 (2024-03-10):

LED Wiring overall

orotecluc, 2024-03-10:
on the ERCF documentation, there is a page on how to wire the ledes individualy for APRON, but nowhere what length the cable towards the MCU should be, nor an explanation n how to wre leds for ERCT..
Would it please be possible to have a bit more detailed information on how to wire up these different LED configurations?

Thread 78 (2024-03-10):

ERCFv2 BOM - Number of filament blocks

alidaf, 2024-03-10:
Many of the v1 kits only had an option for 6 or 9 filament blocks, neither of which are accommodated for in the number of filament blocks selector. Consequently items in the upgrade column won't be suitable for upgrading from v1 for anyone with a 6 or 9 block version.

Closed 2024-03-10.

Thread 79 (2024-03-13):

Filament_Path_xN.stl has 6 non-mainfold edges

relder, 2024-03-13:
Both prusaslicer and orca slicer complain that https://github.com/Enraged-Rabbit-Community/ERCF_v2/blob/master/Stls/Filament_Blocks/Filament_Path_xN.stl has 6 non-mainfold edges and recommends repair.

MissileLaunchSystem, 2024-03-13:
It's a known issue with the built-in supports. If you fix the manifold edges, it makes the supports print as a solid piece instead of hollow, which uses (read: wastes) about a gram more plastic. I'll ask the designer to take a look again.

gneu42, 2024-03-14:
Yes, this know since the very begining. I think it is a fusion 360 bug.
Also, make sure to have the detect thin wall ticked, or you may have no supports.

Just ignore it, as mentioned in the readme file from triple decky github: https://github.com/gneu42/Triple-Decky?tab=readme-ov-file#printing-tips

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

Closed 2024-03-28.

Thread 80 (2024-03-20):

Duplicates in printed parts tracker

Belstrekkie, 2024-03-20:
When selecting the BTT MMB with cotton tail buffer, the '[a]_BTT_MMB_Box_Lid.stl' and '[a]_BTT_MMB_Box_Lid.stl' under 'ERCF_v2 / Recommended_Options / ERCT_Buffer / Stls / Support Arm' are a duplicate of same files under 'ERCF_v2 / STLs / Supports / BTT_MMB / Buffermount_for_ERCT', which are both assigned to be printed.

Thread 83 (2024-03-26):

MMB Can 1.1 does not fit

TravisWilder, 2024-03-26:
Hello
the new MBB Can 1.1 does not fit in the case [a]_BTT_MMB_Box_Lid.stl / [a]_BTT_MMB_Support_Arm_Endcap.stl

kind regards

o1hitman1o, 2024-03-27:
@TravisWilder I curious where are you finding the spects for MMB CAN V1.1? I can't seem to find anything on it.

TravisWilder, 2024-03-27:
I checked the STL which shows 125,448 * 54,4 ... could it be material shrinking?

TravisWilder, 2024-03-28:
I printed again .. now it fits - sorry

Luoti, 2024-04-11:
@TravisWilder What did you do differently the second time, because I'm having the same problem. I already made it work with a chisel though! 😅

Closed 2024-03-28.

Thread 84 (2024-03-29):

ERCT 180 degree coupler issue

bartoszwas, 2024-03-29:
Hey,

ERCT 180 degree coupler block needs and update. Now design is almost perfect when pfe tube goes through whole coupler but nothing holds the tube on other end (not ecas side). Mine printer winded the tube on buffer wheel when filament got stuck on the end of the spool.

I think its just make the hole a bit smaller on the end to keep pfe tube in place.

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

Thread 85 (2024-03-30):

Servo Arm Slippage - Possible Solution

CaptainFoul, 2024-03-30:
Here is a suggested modification to the servo arm to prevent slippage issues with the full printed part.  It is currently in use.

https://github.com/CaptainFoul/ERCFServoArm/tree/main

I don't use Fusion,  so the STEP file changes would need to be ported back to CAD.

billgeek, 2024-08-08:
Thanks for sharing this "mod", I'm about to print this myself (with a small modification of my own) as I started having slippage on the servo arm.

The issue I can see with this is that not all servos are created equal, thus this would require cutting the supplied servo arm to fit.
For example: I purchased an ERCF V2 kit from "Selead Lab" and the provided arms are all longer than the ERCF arm STL:

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

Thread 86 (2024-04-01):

Clear instructions (file list) for Upgrade from 1.1 to 2

jonathanalevi, 2024-04-01:
Perhaps I'm just not finding it, but I don't see any clear instructions for upgrading from 1.1 to 2?

Specifically:

- Which files need to be printed? (Or is it a 100% reprint?)
- Is it a complete disassembly and reassembly? Or can some of the build work be preserved?

I think this would be helpful, as I'm sure we want to enable a smooth upgrade path for 1.1 users...

Thanks!
JL

ningpj, 2024-04-01:
Its pretty much a full reprint and rebuild as its a significant upgrade with allot of changes including encoder, selector cart (spring loaded servo), filament carts (wider, built in filament brakes, no top hat inserts, 2020 mount), integrated bypass end block, 2020 backbone & gearbox changes, etc. There's really only a handful of parts like the 80T printed gear, gearbox cover, motor mount, latches and a few other small parts you can reuse.  The printed parts tracker tracks this however:

https://docs.google.com/spreadsheets/d/1h1bJurR6Z8Ou36c5U9cWmqI86tXKlWrcZrWrHgGN13A

Use Google Sheets "Make a copy" to copy it to your own private google drive, uncheck "Is this a new build?" to exclude reusable parts and review other questions to understand what you need to print.

Points to note, 1) the filament carts are all new, wider than ERCF v1 & mount to a 2020 rail so will need to completely disassemble your ERCF v1 including removing BMG gears from the D-shaft if you plan to reuse it. 2) as the filament carts are wider, longer 8mm and 5mm D-cut shafts are required to build ERCF v2 with the same number of carts you had previously with v1.  The only exception to this is the D-shaft from the ERCF v1 6-cart build as this is just long enough for an equivalent 6-cart build (I know this as this is what I upgraded from). If you have a 9 or 12 cart ERCF v1 you will loose a cart if you plan to reuse your existing D-shaft.  3) you will need a length 2020 rail to rebuild ERCF on.

Required hardware for upgrading is also itemized in the 1.1 upgrade column in the BOM and will look into adding v1.1 upgrade guidance when the readme.md is revised for the next release.

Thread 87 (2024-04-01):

Missing Holes in [a]_Support_Arm_Endcap_No_Electronic_Box.stl in ERCT_Buffer

greyhound3, 2024-04-01:
I have not printed this part yet, but from the looks the 3 hexagonal holes, which the Coupler Block has the standoffs on the right side, could be missing. The stl of the Support_Arm with the electronic box seems to have these holes. But it could also be an error on my side.

greyhound3, 2024-04-01:
They are on the other side, as I suspected, my mistake.

Closed 2024-04-01.

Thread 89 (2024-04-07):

Selector motor mount doesn’t fit motor

igiannakas, 2024-04-07:
The motor supplied with the certified seleadlab kit is a bit too thick to fit in the selector motor mount. Needs around 1mm trimming to allow for enough clearance.

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

rybassv, 2024-05-18:
I think this is a kit supplier fault. Stepper from BOM fits perfectly.

igiannakas, 2024-05-18:
It’s an approved vendor from the ERCF team though…

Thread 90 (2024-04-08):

Filament Block Base built in supports are fragile

ressu, 2024-04-08:
The built in supports in the Filament Block base have a very thin portion at the bottom. Even when the bed adhesion holds up, it's very likely that the thin portion flexes enough for the print to fail:

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

By adding a small support to the very thinnest part makes the print much more reliable (from 16% success rate to 100% success rate)

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

While this is a quick fix for the print, there is another issue with the same built in support where the bottom 2 layers float in air before connecting with the colum that reaches up from the bottom.

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

It doesn't seem that these 2 loose layers reduce reliability noticeably, but sometimes there are artifacts in the print because the supports move around and stick to the parts.

Garethgb, 2024-04-08:
I'm literally just reprinting more of these as 4 failed exactly as described

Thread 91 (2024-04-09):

FR - Galileo 2 Extruder with (2) filament sensors

77arkus76ohr, 2024-04-09:
Hi all,
I was wondering if someone worked or is working on a MOD to have two filament sensors for the new Galileo 2 extruder (G2E) by @jaredC01? He pointed out in his Issue-tracker, that ERCF_v2 is dealing with it?!? https://github.com/JaredC01/Galileo2/issues/36#issuecomment-2030825242

I did not find a hint for the G2E in here. Did I miss it?

I was checking with the last STL of the G2 how to fit a D5H to it. But I wasn't successful. Yesterday I came across the D2H from omron. Maybe this can make it possible? Or did someone else found a solution already? https://omronfs.omron.com/en_US/ecb/products/pdf/en-d2hw.pdf

igiannakas, 2024-04-09:
There are two ways to do this:
1. With d2f switches and bearings: https://github.com/IRTrail/G2E-Filametrix
2. with a d2f lever switch without bearings: https://github.com/rongith/Adaptation-from-Tircown-s-filament-sensor (it replaces the front block).

im using option 2 - less filament drag and an easier print.

both have been updated with galileo 2 final release.

Tyler8299, 2024-04-09:
Something like this?On Apr 9, 2024, at 1:34 AM, 77arkus76ohr ***@***.***> wrote:
Hi all,
I was wondering if someone worked or is working on a MOD to have two filament sensors for the new Galileo 2 extruder (G2E) by @JaredC01? He pointed out in his Issue-tracker, that ERCF_v2 is dealing with it?!? JaredC01/Galileo2#36 (comment)
I did not find a hint for the G2E in here. Did I miss it?
I was checking with the last STL of the G2 how to fit a D5H to it. But I wasn't successful. Yesterday I came across the D2H from omron. Maybe this can make it possible? Or did someone else found a solution already? https://omronfs.omron.com/en_US/ecb/products/pdf/en-d2hw.pdf

—Reply to this email directly, view it on GitHub, or unsubscribe.You are receiving this because you are subscribed to this thread.Message ID: ***@***.***>

Tyler8299, 2024-04-09:
https://github.com/IRTrail/G2E-Filametrix

igiannakas, 2024-04-09:
> https://github.com/IRTrail/G2E-Filametrix

Personally I’m a bigger fan of this front plate: https://github.com/juliusjj25/G2E-Filametrix-Lever-Switch-Mod

as it doesn’t use ball bearings there is less friction in the filament path and it’s less sensitive to micro switch tolerances.  Printed both but ended up with the above.

Tyler8299, 2024-04-09:
I’ve not experienced any issues or added friction in my 3 toolheads  On Apr 9, 2024, at 6:49 AM, Ioannis Giannakas ***@***.***> wrote:

https://github.com/IRTrail/G2E-Filametrix

Personally I’m a bigger fan of this front plate: https://github.com/juliusjj25/G2E-Filametrix-Lever-Switch-Mod
as it doesn’t use ball bearings there is less friction in the filament path and it’s less sensitive to micro switch tolerances.  Printed both but ended up with the above.

—Reply to this email directly, view it on GitHub, or unsubscribe.You are receiving this because you commented.Message ID: ***@***.***>

Tyler8299, 2024-04-09:
sorry I was a bit asleep responding last night here is the version the ERCF team recommends using.  https://github.com/IRTrail/G2E-Filametrix Silverback Attack "ERCF team member" has been working hard making a Flawless Dual Sensor version which has been extensively tested by the team to not create any false positives. Enjoy!

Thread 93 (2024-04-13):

Slicer Settings to print the parts

dushyantahuja, 2024-04-13:
I simply cannot find the recommended slicer settings and material for the printed parts. Can you please point me in the right direction and update the documentation please.

ningpj, 2024-04-13:
ABS. You will find a summary of print settings on pg 4 of the manual. https://github.com/Enraged-Rabbit-Community/ERCF_v2/blob/master/Documentation/ERCF_v2_Manual.pdf

dushyantahuja, 2024-04-13:
Thanks - I swear I read the manual :-)

ningpj, 2024-04-13:
No problem. Easy to overlook.

Closed 2024-04-13.

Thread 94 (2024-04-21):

please provide an CAD step file

fabse-hack, 2024-04-21:
Hello

Can you upload an CAD *.step file from the whole module ?

that would be nice.
f3d is fusion360, i think much people now use onshape or other powerful cad softwares.

Greetings

ningpj, 2024-04-21:
The step file is in the zip.  We can probably rename the zip to make it a bit more obvious however.

Closed 2024-04-21.

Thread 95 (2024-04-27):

Incorrect gearbox sub-assembly part count in manual

mikesmitty, 2024-04-27:
On page 36 of the assembly manual (Gearbox Part 2) the printed parts list says 1x of the bearing spacers is required for the sub-assembly, but points to the assembly diagram that depicts 2x of the bearing spacers

Miriax, 2025-02-04:
Fixed with commit [8977d1a](https://github.com/Enraged-Rabbit-Community/ERCF_v2/commit/8977d1a7bbfa49ea913149ed02d69cff01b2ea61). Thank you!

Closed 2025-02-04.

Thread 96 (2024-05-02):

ERCT Microswitch wiring instructions

digitalirony, 2024-05-02:
The wiring instructions for the micro switch seem pretty off.

It says:
"First, solder a wire (26-28 AWG
recommended) to the Normally Closed
(NC) leg of each microswitch, matching
the length for each gate to the table to
the left. Last (N) is gate closest to the
MMB,
Next, connect the Common (C) legs of
each neighboring switch with a piece of
wire 70mm long.
For the last microswitch in the chain,
solder an additional 110mm wire to the
Common leg, to feed to the MCU."

The Last gate isn't N its N-1, since we start counting at 0.
Also the table with wire lengths should be N- and not N+ since we are counting down and not up.

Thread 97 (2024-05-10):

Introduction / Print Guidelines - update first print file name ERCF_Calibration_Tool.stl to Calib_Test.stl

tiwipewo, 2024-05-10:
Page 4 of ERCF v2 BUILD GUIDE VERSION 2024-04-01, it is referenced a file named ERCF_Calibration_Tool.stl.
This file is not available on the repo, and page 14 the drawing refers to Calib_Test.

markbernard, 2024-08-01:
Found it hear: https://github.com/Enraged-Rabbit-Community/ERCF_v2/blob/master/Stls/Tools/Calib_Test.stl

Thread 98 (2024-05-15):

Wrong hole size on Gear Box Front

gabber130779, 2024-05-15:
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

The holes showen in Picture are to big. the screw M3x20 should go in the plastic, but the hole is 3,1mm. this doesn´t make sense.

ntchris, 2024-07-19:
that hole is for the M3X20mm long screw which goes through the side latch, right?
If you could take a look at the part "gear box back", you can see there is a M3 heat insert to hold that M3 screw.
so the 3.1mm diameter hole doesn't hold the screw, it's not a tap in hole, it just to let the screw go in a bit.

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

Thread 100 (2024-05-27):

Documentation: washers have hex drive

strayr, 2024-05-27:
Page 7 of manual uses the definition of BHCS for a washer.

> WASHER
> Metric fastener with a domed shape head and hex drive. Most commonly found in locations where M5 fasteners are used.

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

Should be something like:
> These are nearly flat stamped steel toroids...

are these even used amymore? It looks like the washer magnet gate stuff is gone?

Miriax, 2025-02-04:
Fixed with commit [8977d1a](https://github.com/Enraged-Rabbit-Community/ERCF_v2/commit/8977d1a7bbfa49ea913149ed02d69cff01b2ea61). Thank you!

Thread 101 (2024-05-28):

ERCT issues with RC2 Coupler_Block_Base and with arm hexagon holes.

adolfotregosa, 2024-05-28:
I reported this on discord
https://discord.com/channels/460117602945990666/909743915475816458/1245146439353372752

But I'll repeat the post here.

All ERCT Coupler_Block_Base versions have a design flaw in my testing. When a spool ends and the filament as a kink, it is capable of pulling the ptfe tube with it.
The Coupler_Block_Base should have a built in bowden tube stopper. My solution for now is a reverse ecas with lock clip so it cannot depress and let the ptfe tube slide inwards.
Second issue is that the filament that was reversed managed to get exactly into the ERCT arm holes and get stuck. That zone of the arm should be solid, without any holes.
Also the RC2 Coupler_Block_Base entrance  does not help inserting the filament. In reality it's still a pain in the ass to insert the filament. The entrance funnel could be a bit more downwards.

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

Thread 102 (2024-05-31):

Documentation of 180 degree option

saeugetier, 2024-05-31:
Please add some documentation about the 180 Coupler option of the ERCT. What is the use of the Magnetic PTFE Coupler and the Arm Anchor?

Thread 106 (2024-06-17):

ERCF V2 Manual - Typo

Ledzpg, 2024-06-17:
I saw an error on page 40. On the exploded view of the gearbox, the correct letter for the bearing is J, not G.

 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

ningpj, 2024-06-17:
Noted. Source document updated for RC2 rework and release

Miriax, 2025-02-04:
Fixed with commit [8977d1a](https://github.com/Enraged-Rabbit-Community/ERCF_v2/commit/8977d1a7bbfa49ea913149ed02d69cff01b2ea61). Thank you!

Closed 2025-02-04.

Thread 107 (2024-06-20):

request to support larger and stronger springy servo

ntchris, 2024-06-20:
request to support larger springy push down servo

feature request to support 28mm length servo or even larger servo ?
thanks.
currently it only supports 23mm servo (22.5mm)
I printed and installed springy for a few months now,
I found that the 23mm wide MG90S micro servo sometimes cannot move to "down" position, because the spring resists and move the arm back.
Maybe the 23mm wide MG90S micro servo is too weak, and cannot provide necessary force to push down the strong spring.
The work around is to tweak with the spring length, cut and try.
and I also have to use 0.8mm dia spring.

There are some slightly larger 28mm wide servo in market with cheap price, should be stronger and better.
for example
https://www.aliexpress.com/item/1005003643468291.html?spm=a2g0o.cart.0.0.5cfb38dapkgguq&mp=1
17g metal gear

Maybe 33mm servo is even better,
or,  36mm or 40mm servo is too large to fit ?
Thanks!

This request was originally opened for Springy project because no step file is available and seems that project was dropped/abandoned.
Now that we have ERCF V2 , the frame is much stronger, and the CAD files are available....seems should make more sense and easier.
Just open this request maybe many other users need it as well.
Thanks.

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

Thanks

MakManIfest, 2024-06-26:
You should be able to find a higher torque servo of the same dimensions as the MG90S.

Servo's mostly have semi standardized dimensions. For the MG90S dimensions you should look for high torque digital servos for use in 450 size R/C helicopter tail and swashplate.

These servos will be high speed and very precise with plenty of torque, 3-4kg. They will either be all metal or mostly metal construction for heat dissipation as the down side of these servos is they usually require high voltage to get the max torque and speed. By high voltage I mean 6-8 volts. But there are some that will run happily at 5v with decreased torque and speed.

During my time flying R/C heli's I tested many different servos and found you get what you pay for. You can save some money by getting a clone of a KST servo. Like this for example. https://www.aliexpress.com/item/1005005625391299.html

ntchris, 2024-08-15:
done.
https://www.printables.com/model/971423-ercf-v2-selector-mod-for-larger-28mm-17g-servo

https://github.com/ntchris/voron_mod_super_diy/tree/main/ercf_v2/servo_28mm_selector

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

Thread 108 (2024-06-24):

Tag plates for ERCT

alidaf, 2024-06-24:
There are no tag plate files orientated the correct way for the front of the ERCT. If you use the tag plates for the ERCF then these will be upside down.

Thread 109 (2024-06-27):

Ender 3 with Sprite Extruder Pro

RobinDadswell, 2024-06-27:
Is it possible to use this with the Sprite Extruder Pro on an Ender 3?

ikomhoog, 2024-07-24:
I am also very interested in this, so I can build the ERCF v2 for my Ender 3 S1 Pro.

I have found and printed https://www.thingiverse.com/thing:6629071, but this had some locking issues.
It also did not really fit with my fanduct.

Because of those 2 reasons I am currently making a remix of it using the filametrix blade holder and lever (with some minor changes).

This is the first time I'm using CAD software so It's taking a bit of time and won't be the prettiest.
I currently have the blade part working (manually) and attached to my printhead as of yesterday, But I still need to add the part that it bumps against to actually push the button.
After that, it's testing for reliability and making adjustments.

Once I have this working I'll post it as a remix on thingiverse and also provide a link here.

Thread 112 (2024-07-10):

Documentation - SUB-BOM Info Missing or Incorrect

sparticvs, 2024-07-10:
On Page 26 for the Gearbox Sub-BOM Part 1, the table is missing for the 2020 extrusion lengths, instead this is found on page 36.

On Page 36 for the Gearbox Sub-BOM Part 2, the table is missing for the D-Cut Rod lengths, and I'm not able to find this anywhere else in the manual.

Miriax, 2025-02-04:
Fixed with commit [8977d1a](https://github.com/Enraged-Rabbit-Community/ERCF_v2/commit/8977d1a7bbfa49ea913149ed02d69cff01b2ea61). Thank you!

Closed 2025-02-04.

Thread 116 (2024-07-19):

filename is wrong - Filament_Blocks/Tag_Plates stl file names has wrong [a] for plate for missing [a] for digits

ntchris, 2024-07-19:
filename is wrong - Filament_Blocks/Tag_Plates stl file names has wrong [a] for plate for missing [a] for digits

currently the Filament_Blocks Tag_Plates stl file names are wrong.
All digits file name has no [a] for accent color,  but they should have [a].
And all the plate file name have a [a], however, it should be primary color, no [a] should be there.
According to CAD file and document,
all digits should be "red" in accent color, therefore, all digits files like Tag_plates_Digit0_x2 Tag_plates_Digit1_x2.stl etc should have [a].

thanks.

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

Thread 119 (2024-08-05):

Documentation Correction: ERCF V2 Manual

AustinTylerDean, 2024-08-05:
Page 98
"ASSEMBLY
Start by fitting the metal rod into Encoder_Right"

I believe that should be Encoder_Left, as the Encoder_right instructions are on the next page.

Page 99

"Screw and self-tap the M3x8 SHCS into the plastic hole"

The picture shows a BHCS.

Miriax, 2025-02-04:
Fixed with commit [8977d1a](https://github.com/Enraged-Rabbit-Community/ERCF_v2/commit/8977d1a7bbfa49ea913149ed02d69cff01b2ea61). Thank you!

Closed 2025-02-04.

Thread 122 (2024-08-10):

CAD for ERF filament cutter depressor mount

ksteddom, 2024-08-10:
Would it be possible to post the cad drawing for the depressor mount for the filametrix? I have steel backing rods rather than titanium or linear rails and the mounting hole spacing is different. Thanks

Closed 2024-08-17.

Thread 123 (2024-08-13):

[Suggestion]: Filamentalist - 606 bearing option for tensioner arm

k1-801, 2024-08-13:
The 608 bearing used in the tensioner arm is quite large for it's purpose. I believe it could be replaced with a smaller and cheaper 606 bearing with only minimal changes to the design and with no consequences.

SkiBikePrint, 2025-01-11:
The 608 bearing for the Tensioner Arm was selected to be the same as the Rim and Idler roller bearings to minimize BOM content.  608 bearing are quite inexpensive on Amazon and Aliexpress.  There is an issue for a limited number of Filament suppliers where the spools are packed full and then the filament roll on a new spool interferes with the 608 on the Tensioner Arm.  For this situation there is a 688 bearing version of the Tensioner Arms.

Closed 2025-01-11.

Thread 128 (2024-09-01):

Motor_Arm_NEMA14,dosent fit aluminum  80 tooth gear

Mark-Zina, 2024-09-01:
In Motor_Arm_NEMA14 there is a cone shaped area where the bearing resides. I have an aluminum 80 tooth gear that came with my kit.The gear has a shoulder that hits the inside of the cone area. The gear's tooth area is 10mm wide and the shoulder where the set screws are is 16mm dia. and protrudes past the tooth area 6.25mm. Is there a fix that already exist for this? If not is there someone who is pretty good with cad who can make the changes and post a new "Motor_Arm_NEMA14 stl"??

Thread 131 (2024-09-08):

[Filamentalist] FAQ documentation refers to unavailable links in rc2 branch

lordofhyphens, 2024-09-08:
https://github.com/Enraged-Rabbit-Community/ERCF_v2/blob/master/Recommended_Options/Filamentalist_Rewinder/Filamentalist_FAQ.md makes several hard links to the HEAD of `rc2` branch, which was taken private 2 months ago. Those links are now dead and causing confusion for people.

Additionally, it's probably not a good idea to have explicit branch references in `master` anyway.

SkiBikePrint, 2025-01-11:
Links corrected.  Thanks!

Closed 2025-01-11.

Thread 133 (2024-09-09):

Missing tool head cable cover file for filamatrix tool head

3D-Magic, 2024-09-09:
Hi Team, not sure if you have noticed, but the cable cover in the filamtrix tool head section is missing the cable cover, I have the one from the original filamatrix repository as well as a vented variant that allows better cooling for the CAN board.

[EBB Cable cover for filamatrix CW2 Toolhead.zip](https://github.com/user-attachments/files/16924309/EBB.Cable.cover.for.filamatrix.CW2.Toolhead.zip)

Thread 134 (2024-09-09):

[Filamentalist] Manual and BOM inconsistent on the screw size

mwiercinski, 2024-09-09:
The [PDF manual](https://github.com/Enraged-Rabbit-Community/ERCF_v2/blob/master/Recommended_Options/Filamentalist_Rewinder/Documentation/Filamentalist_Rewinder_Manual_V3.pdf) mentions  using M3x8 SHCS screws for securing the rollers to the axle shaft, but BOM mentions M3x10.

SkiBikePrint, 2025-01-11:
Although either 8mm or 10mm screw lengths will work, the Readme BOM was updated to M3x8 SHCS to avoid future confusion.  Thanks for pointing this out!

Closed 2025-01-11.

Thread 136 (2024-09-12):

Filamentalist_F1 mod supports under 2020 profile

lpeiro61, 2024-09-12:
I can't find the STL of support parts for under the 2020 profile, for above the table.

SkiBikePrint, 2025-01-11:
Did you get this resolved.  All though I am not the designer of the F1 User Mod version I did look at it and there are no parts that go under the 2020 profile.

Closed 2025-01-26.

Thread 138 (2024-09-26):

Filamentalist rear load option interferes with full spools.

miguelangel-nubla, 2024-09-26:
When using the filamentalist rear load tensioner mount option, the 608 bearing touches the spool filament directly, preventing it from rewinding.

This only happens with a full spool.
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

miguelangel-nubla, 2024-10-11:
Attached quick and dirty solution using a 625 bearing
[Tensioner_Arm.zip](https://github.com/user-attachments/files/17343832/Tensioner_Arm.zip)

Closed 2025-01-04.

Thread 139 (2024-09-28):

Idea for filament cutting to be in the ecf itself

SamueldaCostaAraujoNunes, 2024-09-28:
I had an idea, I don't know if it was considered during the development of Filamentalist. Instead of cutting the filament directly on the SB, couldn't it be done on the ERVF when it finishes retracting? In the Encoder_left and Encoder_right parts, there could be two blades pointing at the filament. When changing color, there would still be a small amount of filament left. When moving to another slot, it would cut off that end. There could be an opening underneath these parts to allow the rest of the filament to be thrown out of the tube. In addition to not having to change an existing SB, this solution would also avoid the need for more extrusion just to eliminate that cut piece. I included a merely illustrative image.

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

norris108, 2024-09-30:
There's the [EREC](https://github.com/kevinakasam/ERCF_Filament_Cutter) which is a selector mounted filament cutter for those that can't or don't want to modify their toolhead

I've been using it for six months now, works great as long as your tip forming is dialled in!

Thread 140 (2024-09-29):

[Sugestion] Coupler Block with 4.5 mm steel ball

klone52, 2024-09-29:
There are cheaper and easier to find 4.5 mm steel balls in airsoft ammunition, with great diameter consistency. For this you would have to move the pre-gate switch closer and decrease the diameter of the hole by 1 mm.

To make it backward compatible with the kit boards you would have to bring the switch closer and make space in this way:

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

Tyler8299, 2024-09-29:
Have u had issues? I have (6) 8 gates built for testing and the bearing and switches have never been an issues

klone52, 2024-09-29:
i bougth my kit from siboor and came with 1 ball bearing 8 mm diam. I'm from Chile and is not easy to find 5.5 mm steel balls. The best alternative i found was the bbs from airsoft guns, and they are pretty cheap , like 500 for  5 USD

Tyler8299, 2024-09-29:
I'm sorry to hear that. Something so simple and readily available mostly around the world. That really does make things a bit difficult for you but most of us can get this overnight or even the same day CHEAP within good tolerances. Have you made the modification already?

klone52, 2024-09-29:
I made it for me and i'm waiting to have spare time to test it. I think in a couple of days i can have it installed on my 8 gates

Tyler8299, 2024-09-29:
Best of luck please keep us posted on how everything works out

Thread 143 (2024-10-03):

Happy Hare+ERCF v2 Install on Nebula pad Ender 3 v3 KE? is it possible?

SPYKE357, 2024-10-03:
Good day everyone,

Hope you are all well.
Has anyone has had any success and if so, how?
sorry to bug you all with this issue of mine but i was wondering if it's possible to install HappyHare for a ERCF v2 kit i bought ( still to build) on the ender3v3ke/nebula pad? i'd like to keep the nebula pad if possible as the only other mcu i have is a pi zero 2(also not sure if there is a full klipper release/build for that printer...
the ke/nebula pad has been rooted and i see the boards are similar/same as the k1. been trying the last couple of days to install it but no luck so far... do you know if it's possible? and if so how and are there any limitations?

if i do this command through ssh "uname -m" it returns "mips" as a response.

-sh: ./install.sh: not found

this is returned when i run the ./install.sh line.

it cloned the happyhare git successfully but wont install. i was hoping it would run the same install paths as the k1 as it also shows mips.

Any and all help will be massively appreciated.

Tyler8299, 2024-10-03:
I'm not saying it can not be done but...... I don't believe any of our team members have this printer to develop for so non of us have worked on it. Everything is mostly focused around Raspberry Pi.

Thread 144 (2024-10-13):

Filamentalist - left/right supports missing hole for baseplate mounting screw

system-dsn, 2024-10-13:
[Left_Support.stl](https://github.com/Enraged-Rabbit-Community/ERCF_v2/blob/master/Recommended_Options/Filamentalist_Rewinder/Stls/Left_Support.stl) and [Right_Support.stl](https://github.com/Enraged-Rabbit-Community/ERCF_v2/blob/master/Recommended_Options/Filamentalist_Rewinder/Stls/Right_Support.stl) are missing the hole for the screw to mount to the base plate.

I checked the CAD file and the holes are there.

CAD: 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
STL:
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

SkiBikePrint, 2025-01-11:
This issue was corrected on 11/21/24 with the V3.0.4 release.  Thanks for your input!

Closed 2025-01-11.

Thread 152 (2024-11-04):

V6 Hotend Filametrix hotend body causing interference with modified CW2 body

halfbro, 2024-11-04:
The STL provided with the Filametrix filament cutter for the V6 hotend ([located here](https://github.com/Enraged-Rabbit-Community/ERCF_v2/tree/master/Recommended_Options/ERF_Filament_Cutter/Stls/Hotends/V6_R6)) has the hotend sitting slightly proud of the surface. This causes interference with the modified CW2 body when the knife blade is inserted, which is deflecting the CW2 body and putting stress on other parts.

As shown here, the current part only leaves a 2.9mm depth hole for the V6 to slot in to:

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

...but in the specifications for the hotend, it's 3.6mm (and has been confirmed in the real world for these "direct drive" style V6 hotends, which are apparently different from the "bowden" style V6 hotends):

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

This 0.7mm of additional height above the flat part is causing some interference issues, and the fix would be to move the mounting flanges down 0.7mm to adjust for this.

probrwr, 2024-12-22:
I too am dealing with this. Additionally what do you put in the top of the V6 to close up the large hole and retain the bowden tube?

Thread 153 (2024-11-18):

Filament and tube generate static electricity then cause mmu board been shock and disconnect. (Potential damage)

willzhai55, 2024-11-18:
I noticed that when mmu loads or unloads filament, the friction can cause an electricity shock to mmu and cause it to disconnect or even stop working. The shock will happen between the tube and the encoder. My encoder stopped working after a few shocks. My solution was to ground the bearing. After this modification, the mmu has never stopped working. I was shocked when I removed the tube form ercf and realized this was the issue.

It might be because I am in Canada and the humidity is around 20%. I did two ercf with three different motherboards It will happen all the time until I ground the bearing. (Also on my voron 0.2 it will shock the filament sensor and cause the mcu to die. Even the soc in some cases. I was absolutely no ideal before and now everything is just much more stable.)

tomlikesrocks, 2024-11-21:
Are you feeling or seeing these static shocks?
I'm in Perth Australia where our humidity is also very low, but I've never experienced a shock before.
However, I have had some disconnection issues.

DarkShadowsX5, 2024-12-04:
You can ground it out by wrapping uninsulated wire around where ever the static is building up and connect it to a ground.
or print it in ESD safe filament since you're in an area prone to Static build up.

SkiBikePrint, 2025-01-04:
I can confirm this is a legitimate issue as I experienced this multiple times back when I used the ERCF EZ board. As an electronics manufacturing engineer, managing static electricity buildup and discharge (ESD) is very important for protecting sensitive semiconductor devices.

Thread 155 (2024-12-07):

SB_G2E_Rear_Body_EBB missing hole

awickham10, 2024-12-07:
Many umbilical mounts make use of a hole that appears to be missing from the G2E rear body on the top right side if you're looking at the rear of your extruder. Do we think these parts are interchangeable, or can a mounting hole be added?

Here's the ERCF_v2 and IRtrail rear body
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

Here's the official Galileo 2 rear body
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

awickham10, 2024-12-07:
Turns out, IRTrail already fixed this. The part in their G2E-Filametrix repo has the mount hole, but a notch where the cutting arm would interfere.

https://github.com/IRTrail/G2E-Filametrix/blob/main/Extruder%20and%20Cutter%20Parts/Twinsor/STL/G2E_Filametrix_Twinsor_Rear.STL

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

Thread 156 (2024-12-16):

Filamentalist 100mm Base has holes in the wrong position

nikpcenicni, 2024-12-16:
[Correct File with proper hole placement](https://github.com/SkiBikePrint/Filamentalist/blob/main/Archive/Filamentalist_V2/Stls/100mm_Axle/Base_Plate_100mm_V2.stl)

The correct file can be found on SkiBikePrint's GitHub repo.

SkiBikePrint, 2025-01-11:
This issue was fixed in the CAD, step, and stl files on 11/21/24 with the V3.0.4 release.  Thanks for you input!

Closed 2025-01-11.

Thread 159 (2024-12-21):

Help failure of fiber retraction

sima35, 2024-12-21:
-use for 2 colors
-It comes out of the extruder without any problems.
-the tube is easy to pass through
-it pulls out about 3 cm above the extruder

[T0] < En <<<<<.... [Ex ... Nz] -102.0mm (e:49.9mm)
20:44
Attempting to recover filament position...
20:44
Parking toolhead at (x:50.0, y:50.0, z:5.2) for pause operation
20:44
idle_timeout: Timeout set to 72000.00 s
20:44
After fixing, call RESUME to continue printing (MMU_UNLOCK to restore temperature)
20:44
MMU issue detected. Print will be paused
Reason: Unload sequence failed: Bowden pre-unload test failed. Filament seems to be stuck in the extruder or filament not loaded.
Occured when changing tool: T0 > T1

Can someone help me?

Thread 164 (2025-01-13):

ERCT - MMB enclosure blocks bypass inlet ECAS

trevjonez, 2025-01-13:
The bypass is a great addition from V1 but the ERCT blocks the inlet making it effectively unusable.

Making the MMB portion of that side plate thicker to add a path for the PTFE to slide thru behind the PCB seems like a fairly simple way to unblock the inlet without requiring any modification to the non printed BOM.

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

norris108, 2025-01-13:
This is a known issue that has been addressed in the upcoming RC2 release

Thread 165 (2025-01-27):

STEP file for SB_G2E_Front_Body_EBB

rssw, 2025-01-27:
Hi!  Really loving this idea and very close to completing my build, but my blade keeps getting stuck after cutting the filament.  The gap between the top and bottom bodies is just a little too tight.  I'd like to shave a little off the bottom of this model, but the STL doesn't import well to my CAD program, it seems the mesh is not complete so it can't create a solid body.

Can someone help me find the STEP file for this part?

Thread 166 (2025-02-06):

[mod] Support direct drive (nema17 & nema14).

DisDis, 2025-02-06:
I found a good mod for ERCF. It would be great if it was added to the mods folder.
https://www.printables.com/model/1037669-ercf2-direct-drive-mount-mod-nema17nema14

"This mod upgrades the ERCF V2 to direct drive, replacing the original motor with a NEMA17. Direct drive improves torque and control, allowing for faster, more reliable filament loading and unloading compared to the original setup. This results in smoother multi-material transitions and better handling of challenging filaments."

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

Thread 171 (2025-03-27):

Filament tied in ERCT Buffer

kktonev, 2025-03-27:
I try different buffer wheels and aslo the experimental:
Recommended_Options\ERCT_Buffer\User_Mods\michaelw7177\Bufferwheel_Long_Bowden_Experimental

I use it with 5 winds on Voron 2.4.

When load it manually - no problem on the firs gate use. After first use of the gate and turn back the filament is going wind over another.
Same happen when it is a long print with same filament. Till now the modified version is better, but happen friquently to become too thight layers and the extrusion became non stable a little bit.

Next thing is to try to shorten the bowden a little bit and make it work with only 4 winds. Should be better.

If any other solution will be happy to try it.

norris108, 2025-03-27:
The rule of thumb for the number of loops around the buffer wheel is:

Bowden Length / 230 rounded up

How long is your bowden?

kktonev, 2025-03-27:
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

Probably didn't measure it correct - 750-800mm.  But 4 winds are too short - after eject the filament has few centimeters outside the buffer. There is some reserve to cut a piece of the tube and to stay with 4 winds.
Filament has some tension, because it comes from dryer inside of PTFE tubes, but this tension is not so much to make wind overlaping.

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

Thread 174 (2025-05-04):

The new BTT MMB CAN v2.0 does not fit on the erct mount

jellenijhof12, 2025-05-04:
The new BTT MMB CAN v2.0 does not fit on the erct mount.
Is there maybe something i'm missing? Like a altered stl file to make this work.

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

nsrogers, 2025-05-27:
Ran into this also. I found a few remixes on printables and ended up going with this one.
https://www.printables.com/model/1233564-ercf-v2-erct-support-arm-endcap-for-btt-mmb-can-v2

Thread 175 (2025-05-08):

Assist please

hreality, 2025-05-08:
Could you provide a file for fusion with your alterations for the coupler block so I could modify for a project.  I have to extend the rear wall and hook for the PCB outward by @5mm.  Thank you for your time

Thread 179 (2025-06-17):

Support_Arm_xN is different

steirerman, 2025-06-17:
The connection between the cupler arm and Support_Arm_xN is different. Is that correct? the Files is in\Recommended_Options\ERCT_Buffer\CAD\STEP\Support_Arms\ [a]_Support_Arm_xN.stl

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

and in \Recommended_Options\ERCT_Buffer\CAD\STEP\working_files\a_Support_Arm_xN_v21.stl, see the red rectangle

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

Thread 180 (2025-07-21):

katapult menuconfig make

waffled1234, 2025-07-21:
after i have completed the menuconfig
and writen the command 'make'
it comes up with:
        compiling  out/src/sched.o
make: arm-none-eabi-gcc: No such file or directory
make: *** [makefile:71: out/src/sched.o] error 127

does anybody know a fix for this, i am a beginner coder and not very familiar with rasberry pi or python. using BTT MMB CAN V2 and raspberry pi 3.

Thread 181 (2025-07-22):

Help Needed: Seeeduino XIAO Not Showing Up on USB After Flashed Firmware

ItzEarthy, 2025-07-22:
Hi everyone,

I’m trying to flash firmware onto my Seeeduino XIAO using a Raspberry Pi as the host, following instructions from the ERCF Easy-BRD GitHub. However, I’m stuck because my XIAO is not showing up as a USB device on any computer or the Pi itself.

Here’s what I’ve tried so far:

Connected the XIAO via USB-C to Raspberry Pi

Checked lsusb on all machines; the XIAO never appears.

Looked for /dev/ttyACM0 or similar device nodes; none show up.

Tried to enter bootloader mode by shorting the RST and GND pins twice quickly—no USB device shows after. No flashing light.

Tried different USB ports and cables.

it worked up until i did the flash. then i couldn't see it anymore when i went to find the serial number

norris108, 2025-07-24:
Issues in this repo are for reporting problems with ERCF parts

Closed 2025-07-24.

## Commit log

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2023-05-07 removed obsolete insert bearing & feet
    not compatible/obsolete with 2020 extrusion
    [[a]_Bearing_Insert_Feet_x2.stl, [a]_Bearing_Insert_x2.stl]
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2023-05-07 updated gearbox parts
    - Removed overhanging fastener mounting point
    - Added additional mounting points for gearbox
    - Added cable routing holes for bottom panel
    [Gear_Box_Back.stl, Gear_Box_Front.stl, [a]_Bottom_Panel.stl]
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2023-05-07 updated top hat
    - Moved magnet position to match filament block
    - Added optional integrated top hat
    [[a]_Top_Hat_Integrated_xN.stl, [a]_Top_Hat_xN.stl]
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2023-05-07 Updated filament block
    - Mounts directly to 2020 extrusion
    - Top hat magnet position moved over to avoid mounting screw
    - Changed printing orientation, added pre-supports
    - Added a MR85ZZ bearing
    - Changed lever design to reduce supports needed
    [Filament_Block_xN.stl, [a]_Latch_xN.stl]
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2023-05-07 Update README.md
    added note about reinforced gearbox & integrated filament passthrough to component changelog.
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2023-05-09 Added v1 of Springy Servo Mount and associated parts. Removed incompatible components including Top Hats and replaced with Universal Top Hat
    [12mm_Spring_Extension.stl, Gate_Key.stl, Savox_Adapter.stl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]
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2023-05-09 Fixed printing orientation of new parts
    [Idler_Block.stl, Selector_Door.stl, Servo_Mount_Savox.stl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]
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2023-05-09 Base_beta3_1 is now layer compliant.
    Made Base Beta3.1 layer compliant.
    Add support for second magnet
    Modify support for tag plate
    [Triple_Decky_Base_Beta3_1.stl]
2023-05-09 Correct support
    For unknown reason the support was not hollow.
    [Triple_Decky_Base_Beta2_5.stl]
2023-05-10 Correct orientation.
    [Triple_Decky_Base_Beta3_1.stl]
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2023-05-11 v24 - fixed servo arm screw position
2023-05-12 Add Trap version of Triple Decky
    Rename Triple Decky as Rev B
    Add Rev C
    [Triple_Decky_Base_Beta3_1.stl, Triple_Decky_Base_xN_C2.stl, Triple_Decky_Filament_path_Beta2_5.stl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]
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2023-05-17 Major naming rework; Updated selector cart and filament block bypass
    [2020_Mount.stl, 2020_Mount_Mirrored.stl, 3030_Flat_Mount.stl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]
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2023-05-17 Update EncoderCart to v179
    - make LED Channel „Face“ 1mm thicker/stronger
    - add new pyramid shaped slotted wheel
    - readd missing hole for endstop screw
    [Encoder_Left.stl, Encoder_Right.stl, Encoder_Slotted_Wheel.stl]
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2023-06-02 Correct print orientation
    [Trapy_Tag_plate_10_RevD4_x2.stl, [a]Trapy_Tag_plate_Digit10_RevD4_x2.stl]
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2023-06-11 EncoderCart - Binky v193
    - PCB -0.1mm on Z
    - 0.1mm more diameter of Slotted Wheel
    - 0.1mm thinner slotted wheel cover
    - Changed Slotted Wheel geometry
    - mirror flared filament paths
    - 2.0mm spring thickness
    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
    [Encoder_Left.stl, Encoder_Right.stl, Encoder_Slotted_Wheel.stl]
2023-06-13 EncoderCart Binky v197
    - add version with and without magnet
    - improve spring connection peg
    [Encoder_Left.stl, Encoder_Right.stl, Encoder_Right_with_magnets.stl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]
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2023-06-14 A bit of cleanup of repo - primarily CAD area. Updated the master v2.0 STEP file
    [ERCF Binky v30.f3z, Filament_block_Trapy_RevD3.step, Filament_block_Trapy_RevD4_v13.step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]
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2023-06-14 Updated Stls for Filament end block and moved prototype work into separate directory
    [Filament_Block_End_Bypass.stl, Filament_Block_xN.stl, Filament_Blocks_End_Bypass.stl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]
2023-06-14 EncoderCart Binky v202
    - decrease hole in left spring to grip tight on the idler bearing screw
    [Encoder_Left.stl, Encoder_Right.stl, Encoder_Right_with_magnets.stl]
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2023-07-06 EncoderCart - Binky v214
    - enlarged clearance for BMG gear and BMG Shaft
    - enlarged clearance for Slotted Wheel
    - change slotted wheel from 11 to 12 tooth
    - enlarge ee-sx1103 clearance by 0.05mm
    [Encoder_Left.stl, Encoder_Right.stl, Encoder_Right_with_magnets.stl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]
2023-07-06 fix slotted wheel
    [[black]_Encoder_Slotted_Wheel.stl]
2023-07-08 EncoderCart - Binky v217
    - fix cutout for PCB Headers that got broken in the last version
    [Encoder_Left.stl, Encoder_Right.stl, Encoder_Right_with_magnets.stl]
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2023-07-10 Update TD RevC5 for magnet to RevC6
    2 more perimeters around the bearing (base part)
    Back face angled by 4°
    [TD_Base_Trap_C5_Screw.stl, TD_Base_Trap_C5_V-Shape.stl, Triple_Decky_Base_C6_0.stl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]
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2023-11-03 Correct links
    [Filament_Block_End.stl, Filament_Bypass.stl, Selector_Motor_Support_bushing.stl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]
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2023-11-14 Update ERCF_V2.0.step
    Added roll-in nuts and a couple of missing M3 screws.
2023-11-16 Added Missing Hardware
    Added the missing M5 bolt and locking nut for the bottom half of the hinge. Replaced the wrong M3x12 with M3x25 in the gearbox.
2023-11-17 Renaming and moving some files
    Reorganized some files in the Cotton Tail folder, adjusted some names, and moved the BTT_MMB mounts into the support folder.
    [[a]BTT_MMB_Bottom_Bracket.stl, [a]BTT_MMB_Top_Lid_180.stl, [a]BTT_MMB_Top_Lid_Standard.stl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]
2023-11-17 Spelling Corrections
    Spelling corrections for two part names.
    [Belt_Tensioner.stl, [a]_Integrated_Tophat.stl]
2023-11-18 Update ERCF_V2.0.step
    Renamed all components to match their STL file names. Minor rearrangement of files. Screw length corrections and alternate screws for the drag chain.
2023-11-19 new experimental parts and replacement spring
    New experimental parts to try:
    Anchors for right angle 180 degree coupler - [a]arm_anchor_ptfe
    right angle coupler block - coupler_block_180
    4 degree outlet coupler block - coupler_block_angled
    new updated/replacement spring that shouldn't error on various slicers now.
    [[a]arm_anchor_ptfe.stl, coupler_block_180.stl, coupler_block_angled.stl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]
2023-11-20 New LED jig by Jose
    LED jig tool for the MMB version of the coupler block
    [LED_Soldering_tool_holder.stl, LED_Soldering_tool_holder_by_jose.stl]
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2023-11-27 Update support folder with new Rear Mount box
    Electronics box rear mount edition. I've depreciated the old mount under the encoder for this version.
    [[a]BTT_MMB_Bottom_Bracket.stl, [a]BTT_MMB_Top_Lid_180.stl, [a]BTT_MMB_Top_Lid_Standard.stl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]
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2023-11-28 Added back CAD for NEMA17 Pulley Tool
    Added back recreated STEP file for NEMA17 Pulley Tool.
    [NEMA17 Tool v2.step]
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2023-11-28 fixed problematic overhang on underside of foot
    [[a]_End_Bypass_Foot.stl]
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2023-11-29 corrected stl naming of transparent lens of led front apron
    [[t]_Cover_Lens_No_Support_xN.stl, [t]_Cover_Lens_With_Support_xN.stl]
2023-11-29 Delete Filament_Path.stl
    Delete Filament_Path.stl (it is from Thumper Blocks and doesn't belong here).
    [Filament_Path.stl]
2023-11-30 Renamed Tools
    Renamed some of the Tool STL files to shorten, clarify, and standardize names to Camel_Case.
    [80T_Cog_Guide.stl, Bearing_Install_Tool.stl, Slotted_Wheel_Push_Tool.stl]
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2023-12-02 Update Encoder_Left.stl
    Updated position for Encoder_Left to be in the correct printing position.
    [Encoder_Left.stl]
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2023-12-04 ERCT CAD Remake
    Uploaded new CAD files for ERCT, as 3MF files, for comparison to old STLs.
    [[a]BTT_MMB_case_top.3mf, [a]BTT_MMB_support_arm_bottom.3mf, [a]_Coupler_Block_MMB_xN.3mf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]
2023-12-04 Adding BTT MMB Case files
    Added 3MF versions of the new BTT MMB case files.
    [[a]BTT_MMB_case_top.3mf, [a]BTT_MMB_rear_mount_bottom.3mf, [a]BTT_MMB_support_arm_bottom.3mf]
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2023-12-05 CAD Fixes
    Reoriented the Coupler Blocks to be correct. Re-exported Support Arm.
    [[a]_Support_Arm_xN.3mf, coupler_block_MMB_180.3mf]
2023-12-05 CAD Updates
    Replaced ERCT CAD assemblies with latest files.
2023-12-05 New CAD
    Added a fresh STEP file to fix the missing slot in Support Arm Endcap with Electronics, everything else unchanged. Added Fusion360 project file for editing.
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2023-12-09 CAD redo on Calibration Test
    Redone STEP file for the Calibration Test.
    [Calib_Test_redux.step]
2023-12-09 Update README.md
    Fixed a couple of typos
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2023-12-09 Updated Coupler Blocks 3MF files
    Updated the Coupler Blocks 3MF files to add the hex key pattern.
    [[a]_Coupler_Block_MMB_180_no_switch_xN.3mf, [a]_Coupler_Block_MMB_no_switch_xN.3mf]
2023-12-09 Updated Coupler Block STLs
    Updated to the latest Coupler Block STLs, with no microswitches.
    [[a]_Coupler_Block_180_xN.stl, [a]_Coupler_Block_xN.stl, tobereplaced_[a]_Coupler_Block_180_xN.stl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]
2023-12-09 ERCT / F3D Folder Cleanup
    Cleaned up and renamed F3D files in ERCT CAD folder.
    [Axle_parametric.f3d, Buffer_Wheel_xN.f3d, Coupler_Spring_xN.f3d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]
2023-12-09 Moved 180 degree Coupler Block
    Moved 180 degree Coupler Block to its new home.
    [[a]_Coupler_Block_180_xN.stl, tobereplaced_[a]_Coupler_Block_180_xN.stl]
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2023-12-10 Typo Correction
    Typo Correction. Integrated_Tophat -> Integrated_Tophat_xN
    [[a]_Integrated_Tophat_xN.stl]
2023-12-10 Update [a]_Coupler_Block_180_xN.stl
    Update Coupler Block 180 to have wider filament path, to match other coupler block
    [[a]_Coupler_Block_180_xN.stl]
2023-12-10 Update the MMB Case
    Updated the MMB case to actually fit the MMB and to use zip tie hinges, and updated everything that the MMB case touches.
    [[a]BTT_MMB_case_top.f3d, [a]BTT_MMB_case_top.stl, [a]BTT_MMB_rear_mount_bottom.f3d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]
2023-12-10 Fixed naming conventions
    [[a]_BTT_MMB_Bottom_Bracket.stl, [a]_BTT_MMB_Case_Top.3mf, [a]_BTT_MMB_Case_Top.stl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]
2023-12-11 Added missing underscore
    Added missing underscore to filenames.
    [[a]_BTT_MMB_Case_Top.stl, [a]_BTT_MMB_Support_Arm_Bottom.stl]
2023-12-11 Update Filename Prefixes
    Updated filename prefixes to match Voron standards:
    [o] for opaque
    [c] for clear/transparent
    [mm] for multimaterial
    [[c]_Cover_Lens_No_Support_xN.stl, [c]_Cover_Lens_xN.stl, [mm]_Selector_Door.stl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]
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2023-12-11 Orientation Correction
    [[a]_LED_Carrier_xN.stl]
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2023-12-15 Added missing Stls for toolhead variations making each directory complete
    [CW2_Plate.stl, [a]_CW2_Latch.stl]
2023-12-15 Fixed orientation and naming of Toolhead Stls
    [CW2_Body.stl, CW2_Plate.stl, SB_CW2_Body.stl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]
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2023-12-15 LED Soldering Jig
    Added LED soldering jig CAD and my reworked version.
    [LED_Soldering_Tool.f3d, LED_Soldering_Tool_24mm.f3d, LED_Soldering_Tool_24mm.stl]
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2023-12-18 Add Tools
    Added a couple tools and STLs / CAD for them
    [Filament Block Bearing Insert Tool.f3d, Filament Block Bearing Insert Tool.step, PTFE Tool.f3d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]
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2023-12-19 Even newer Master CAD!
    Changes:
    -Aligned Coupler Blocks with mounting pegs
    -Fixed PTFE to be roughly the correct length and shape. It's not perfect, if anyone can do better, please do.
    -Fixed collision between Bypass block and endcap arms
    -mystery hardware possibly left out of the STEP file (invisible when exported)
    -Lots of tiny tweaks
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2023-12-19 Redesigned LED Carrier to match wiring pattern for front Apron
    [[a]_LED_Carrier_xN.stl]
2023-12-19 Redesign LED Carrier to match Apron LED wiring.
    [[a]_LED_Carrier_xN.stl]
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2023-12-21 Update README.md
    FIxed CAD link
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2023-12-22 Update Encoder_Left.stl
    Fix print orientation.
    [Encoder_Left.stl]
2023-12-22 Update [a]_BTT_MMB_Support_Arm_Endcap.stl
    Fixed missing mounting hole.
    [[a]_BTT_MMB_Support_Arm_Endcap.stl]
2023-12-22 Final tweaks to README. Updated links and videos. Fixed link in manual to Happy Hare
    [Motor_Arm_NEMA14_GS-6pins.step, Motor_Arm_NEMA17_GS-6pins.step]
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2023-12-22 Update README.md
    Fixed Printed Parts Tracker link
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2023-12-22 Correct file and orientation for support arms
    [[a]_Support_Arm_Mount_xN.stl, [a]_Support_Arm_xN.stl]
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2023-12-22 Corrected Exports
    [[a]_Support_Arm_Mount_xN.stl, [a]_Support_Arm_xN.stl]
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2023-12-23 Fixed missing hex key registration parts
    [[a]_Coupler_Block_180_xN.stl]
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2023-12-30 Update README.md
    Fixed link to Happy Hare Landing page
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2024-01-01 Updates to Manual - NEW LED Carrier Option
    Edits, corrections and modifications to wiring diagram and manual. New LED Carrier to accept Apron LEDs
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2024-01-04 Update [a]_BTT_MMB_Support_Arm_Endcap_Bunny_Outline.stl
    Re-add missing features to the STL.
    [[a]_BTT_MMB_Support_Arm_Endcap_Bunny_Outline.stl]
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2024-01-05 Update SB_Bambu_Cutting_Printhead_Back.stl
    Fixed print orientation.
    [SB_Bambu_Cutting_Printhead_Back.stl]
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2024-01-23 Update [a]_BTT_MMB_Support_Arm_Endcap_Bunny_Outline.stl
    Fixed mounting arm length.
    [[a]_BTT_MMB_Support_Arm_Endcap_Bunny_Outline.stl]
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2024-02-14 Print Orientation Corrected - Coupler Block LED Carrier
    [[a]_LED_Carrier_xN.stl]
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2024-03-13 Gearbox and End_Bypass Tweaks
    Added Ark's modifications to address issues #37 (mounting screws hitting the 2020) and #64 (gearbox wiring clearance).
    [End_Bypass.stl, Gear_Box_Back.stl, Gear_Box_Front.stl]
2024-03-18 Update Holder_COAS.stl
    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
    [Holder_COAS.stl]
2024-04-01 Update Holder_COAS.stl
    Update tolerance on Holder_COAS
    [Holder_COAS.stl]
2024-05-19 Update Holder_COAS.stl
    Fix Print Orientation
    [Holder_COAS.stl]
2024-05-22 Update Holder_COAS.stl
    Fix tolerance on Holder_COAS
    [Holder_COAS.stl]
2024-06-10 Remove C7 no supports to avoid confusion.
    [Base_No_Support_xN.stl, Filament_Path_No_Support_xN.stl, [a]_Tophat_No_Support_xN.stl]
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2024-08-08 V3.0.1
    No reprint/rebuild required:
    Improved clearances and print-in support breakaway for Tensioner Arm parts
    Provided additional edge chamfering to Idler Roller Axles
    [Center_Drive_Roller.stl, ECAS_Clip.stl, Idler_Roller_(female)_100mm.stl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]
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2024-08-09 V3.0.1
    Cleaned up Tensioner Mount and 2020 Clip-In support CAD artifacts.
    Did not affect printing but did show up as errors.
    [Left Support_2020_Clip-In_[option].stl, Left_Support_[2020_Clip-In_option].stl, Right_Support _2020_Clip-In_[option].stl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]
2024-08-09 Delete [a]_Tensioner_Mount_with_Sensor_80mm.stl
    Didn't belong in CAD folder
    [[a]_Tensioner_Mount_with_Sensor_80mm.stl]
2024-08-09 V3.0.1
    fixing file names
    [Extended_Support_Filamentalist_Enclosure_Far_Left_[option].stl, Extended_Support_Filamentalist_Enclosure_Far_Right_[option].stl]
2024-08-09 Delete Recommended_Options/Filamentalist_Rewinder/Stls/Support_FIlamentalist_Enclosure_Left_[option].stl
    replacing with corrected filename
    [Support_FIlamentalist_Enclosure_Left_[option].stl]
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2024-10-08 V3.0.3
    1. Updated all component orientations to align to recommended printing orientation.
    2. Included 688 Bearing version/option of Tensioner Arms and alternate printed 16mm Bushing (as alternative to a 688 bearing) to provide clearance where the Tensioner Arm 608 bearing was interfering with the filament on a new fully packed 200mm spool.
    [16mm_Bushing_688_Bearing_[option].stl, Axle_Depth_Tool_100mm.stl, Axle_Depth_Tool_80mm.stl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]
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2024-10-22 tube connector error fix
    ecas04 and 6mm collet option
    [TubeConnector.stl, TubeConnector_6mmCollet.stl, TubeConnector_ECAS04.stl]
2024-10-25 fix accel stl
    [Accel.stl, Accel_rev2.stl]
2024-10-26 V3.0.4
    Supports missing base mounting holes
    [Left_Support.stl, Right_Support.stl]
2024-11-22 V3.0.4
    Fixed issue in parametric model that resulted in misaligned holes in Base_Plate parts for widths wider than for an 80mm axle.
    [Base_Plate_100mm.stl, Base_Plate_100mm_[option].stl]
2024-11-22 V3.0.5
    Additional fix to parametric model for Base Plate mounting holes.
2024-12-02 Update Filamentalist_Rewinder_Manual_V3.1.1.pdf
    Fix build video link in manual
2025-02-04 Updated Assembly Manual
    1. Added clarification to Tuning section that filament should feed through the slot in the Tensioner Arm "nose".
    2. Added a Questions, Troubleshooting, and Help page to end of document pointing to the FAQ and Troubleshooting documents on Github, the tight 1-way bearing heat rework video, and the Filamentalist Discord channel.
2025-02-05 Update readme.md
    Corrected BOM o-ring OD from 26mm to 27mm
2025-02-05 Update readme.md
    Correct BOM o-ring OD from 26mm to 27mm
2025-03-12 V3_beta_v122
    Added Filamentalist_V3_beta folder and 1. CAD files.
    2. Move F1.02v user mode to archive as it had fundamental functional problems. The v3 beta will ultimately replace both the F1_0.01 and F1_0.02 user mods.
    [Accel.stl, Accel_rev2.stl, BearingMount_x4.stl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]
2025-03-12 v124 Beta CAD files
    fixed an error with the parametric model and provided step files for both the 608 and 688 axle bearing versions.
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2025-03-24 Updated CAD
    1. Fixed unconstrained sketches for Chassis
    2. Corrected misaligned locating pegs in Tensioner Mount and Chassis parts
    3. Raised standalone mount for improved bottom feed clearance.
2025-03-24 Corrected Misaligned Bottom Mount Reference Tensioner Arm
    No functional issues, just an aesthetic/visual correction in the CAD
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2025-03-28 Moved Original F1 User Mod to Archive Folder
    Has incorrect filament path for effective Tensioner Arm lifting. V3 will replace the F1.
    [12mmFrontWheelx2.stl, 12mmRearWheelx2_rev3.stl, 15mmFrontWheelx2.stl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]
2025-03-29 Update Hardware-Calibration.md
    Fixed typo and verbiage of the MMU_CALIBRATE_BOWDEN section
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2025-04-02 CAD v212
    Removed Tensioner Arm pivot mounting points/material from Chassis side parts as they are no longer needed.
2025-04-05 Fixed CAD STEP file names
    688 and 608 file names were reversed
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2025-04-18 v241
    1. Increased 1-way bearing press fit hole diameter in CDR from 14mm to 14.2mm.
    2. Increased outer diameter of 688 Bearing Bushing by 0.1mm.
    3. Slotted the tubing pass-thru hole in the Filamentalist Enclosure Rear Mounts to provide more range to align to existing enclosure holes.
    4. Some light CAD file "house keeping", removing obsolete/broken features (none affect existing parts).
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2025-04-21 v26
    Cleaned up CDR Printed Clutch optional subassembly to get rid of CAD errors.
    Tweaked optional CDR Printed Clutch Pawl part for improved engagement
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2025-04-27 FV3 beta v55.1
    Added corrections/clarifications to manual v0.1
    Corrected Tensioner_Mount_Std.stl to include the built-in support
    Included ECAS_Clip_[optional_print].stl file for those who didn't buy or get clips with their ECAS04 parts
    [ECAS_Clip_[optional_print].stl, Tensioner_Mount_Std.stl]
2025-04-27 FV3 beta v55.1
    Corrected Tensioner_Mount_Std.stl to include built-in support
    [Tensioner_Mount_Std.stl]
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2025-05-03 Update Tensioner_Mount_Microswitch_[option].stl
    Was missing the support for the Tensioner Arm (sorry team...)
    [Tensioner_Mount_Microswitch_[option].stl]
2025-05-03 Added missing microswitch option parts
    [6x3_Magnet_Holder.stl, Printed_Switch_Lever.stl, Tensioner_Mount_Microswitch_[option].stl]
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2025-07-07 Updated CAD v1.1.1
    v1.1.1 Changes - No reprints/rebuilds required:
    1. Corrected artifacts on Tensioner Arm pivot mounting hole.
    2. Thickened inner lip of Rim Roller due to some people experience cracking while installing rubber bands.
    3. Inset bearing contact face on Rim and Idler Rollers by 0.5mm to account for previously thickened bearing pocket stop/lip on R/L Chassis parts.
    4. Extended bearing contact faces on Idler Axle by 0.5mm on each end to account for previously thickened bearing pocket stop/lip on R/L Chassis parts.
    [Idler_Roller_Axle.stl, [a]_Idler_Roller_608_Bearing_x2.stl, [a]_Idler_Roller_688_Bearing_x2.stl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]
2025-07-07 CAD v1.1.1
    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
2025-07-22 V1.0.2
    Revised Parametric CAD to correctly display panel sizes based on selected extrusion length.
